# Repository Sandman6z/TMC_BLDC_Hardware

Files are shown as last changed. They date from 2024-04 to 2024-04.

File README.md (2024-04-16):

# TMC_BLDC_Hardware
TMC_BLDC 电路板部分

## TMC_BLDC
[TMC_BLDC 软件部分](https://github.com/Sandman6z/TMC_BLDC)

[TMC_BLDC HAL](https://github.com/Sandman6z/TMC_BLDC_HAL)

## BUGList:
- v1.1

| No. | BUG | Check |
| :-: | --- | :---: |
|  1  | add 12V, 5V, 3.3V test pad | √ |
|  2  | remove HALL | × |
|  3  | remove Q8 | |
|  4  | remove R65 | √ |
|  5  | Change PMOS package (Q1), Rgs (R27), Rg (R24), R14, R15 | √ |
|  6  | Crystal & capacitor package | √ |
|  7  | Inner Power layer shrinks 15mil | √ |
|  8  | LDO current change from SOT-223 to SOT-89 | √ |
|  9  | Add a current sense resistor to one phase due to DC offset | √ |
| 10  | Consider adding a power input fuse | |
| 11  | Replace reset circuit with CAT809 chip | √ |
| 12  | Add a resistor in series with an active crystal oscillator, and paralleling a large capacitor with a FB | |
| 13  | Add an LED in a specific location if have space | |
| 14  | Add Turbo Temp Port | × |
| 15  | Add TMC Debug Port | √ |

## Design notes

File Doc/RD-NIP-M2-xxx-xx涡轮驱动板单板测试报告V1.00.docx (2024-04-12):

| | | 文件级别： 机密 / Confidential | | 共 10 页

项目名称 / Project Name:

NIP

文件名称Doc. Name/编号NO:

涡轮驱动板单板测试大纲/ RD-NIP-M2-xxx-xx

相 关 文 档 / Refer Document
文件编号/Document NO | | 文件名称/Document Name | | | | 版本/Rev.
/ | | 硬件系统设计说明 | | | | 1.00
/ | | / | | | | /
/ | | / | | | | /

文 档 记 录 / Document History
版本/Rev. | 编制/日期 Author/Date | 审核/日期 Checked/Date | | 审核/日期 Checked/Date | 批准/ 日期Approved/Date
1.00

谊安公司（非公开）版权所有

本文件为谊安公司的专有资料。任何对本文件的使用、复制、或发布行为均是明确禁止的，除非本公司特殊批准，否则将被视为侵犯本公司的权利和利益。

©AEONMED CORP. (UNPUBLISHED)ALL RIGHTS RESERVED

This material is the proprietary information of Aeonmed Corp. and any use, reproduction, or distribution of the material contained herein, unless specifically authorized by Aeonmed Corp., is expressly forbidden and would violate the rights and interests of Aeonmed Corp..

版本 | 描述 | 编制/日期
1.00 | 初始版本 | 张宝宁 2024.1.25

# 目录

# 第1章 设备与环境

## 1.1 测试设备

序号 | 测试设备 | 数量
| 稳压电源 | 1台
| 数字万用表 | 1台
| 示波器 ，500M带宽，具有存储功能 | 1台
| 测温仪 | 1台
| PC机及监控软件 | 1台
| 信号发生器 | 1台
| 直流电源分析仪 | 1台
| 测试工装（NIP电源板V2.00，压力传感器160MDAA5，瑞士涡轮U65HN-024KS-6，风扇12V0.5A四线） | 1套
| 热风枪 | 1台

## 1.2 电路板硬件软件信息

序号 | 栏目 | 详细信息
| 硬件电路版本 | 45200xxxx #NIP涡轮驱动板V2.00 SN：
| 测试软件版本 | TMC_BLDC_ NIP涡轮驱动板V2.00
| 其它软件 | 无

## 1.3 测试环境

除非特别声明，一般测试环境为：

温度：20～25摄氏度

湿度：30％～85％

高度：－100～＋100m

# 第2章 测试内容

## 2.1 电压测试

测试涡轮驱动板各电源电压。

测试栏目 | 判据 | 测试数值 | 结果
VIN | 电压：24.7V±1% | 24.43V | PASS

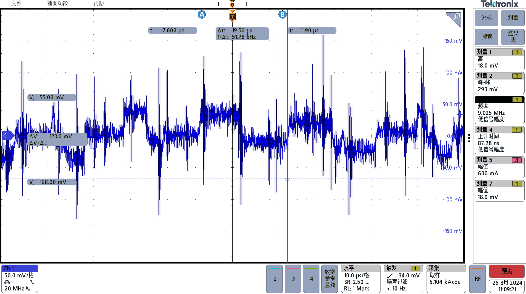
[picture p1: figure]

12V | 12±0.2V 纹波：20MHz带宽<120mV，记录数值和波形 500MHz带宽只记录数值和波形 | 12.21V | 纹波波形异常 Vp-p = 290mV

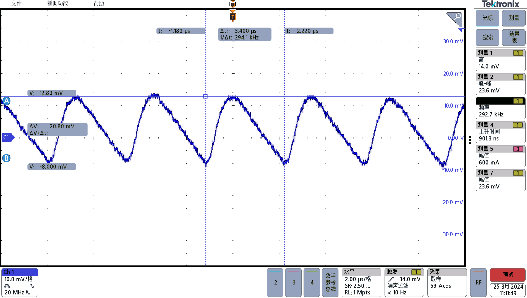
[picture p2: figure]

5V | 5±0.1V 纹波：20MHz带宽<50mV，记录数值和波形 500MHz带宽只记录数值和波形 | 5.06V | PASS Vp-p = 23.6mV

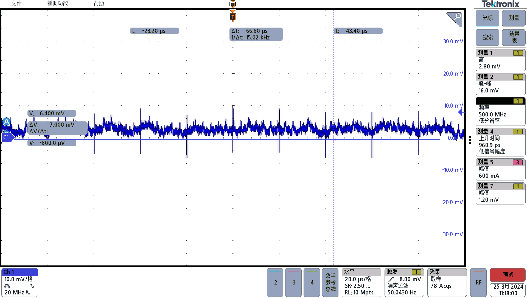
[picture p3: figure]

3.3V | 3.3±0.1V 纹波：20MHz带宽<33mV，记录数值和波形 500MHz带宽只记录数值和波形 | 3.28V | PASS Vp-p = 16mV

## 2.2 转速测试

控制输入0.5-4.5V电压，对应线性关系，6667rpm到60000rpm转速，误差±2%（对空吹时最高转速>50000rpm即合格）。

待测电压V/转速理论值rpm | 测试值对空rpm | 误差% | 测试值堵死rpm | 误差% | 结果
0.5V/6667 | 6666 | -0.015% | 6666 | -0.015%
1.0V/13333 | 13332 | -0.008% | 13332 | -0.008%
1.5V/20000 | 19998 | -0.010% | 20004 | 0.020%
2.0V/26667 | 26664 | -0.011% | 26670 | 0.011%
2.5V/33333 | 33336 | 0.009% | 33354 | 0.063%
3.0V/40000 | 39996 | -0.010% | 40002 | 0.005%
3.5V/46667 | 46656 | -0.024% | 46674 | 0.015%
4.0V/53333 | 53304 | -0.054% | 53334 | 0.002%
4.5V/60000 | 55770 | -7.050% | 57090 | -4.850%

## 2.3 电流波形测试

设定涡轮一定转速，使用示波器电流探头测试任意一个相线的电流波形，应为近似正弦波，记录三个不同转速下的波形。

转速 | 波形 | 结果

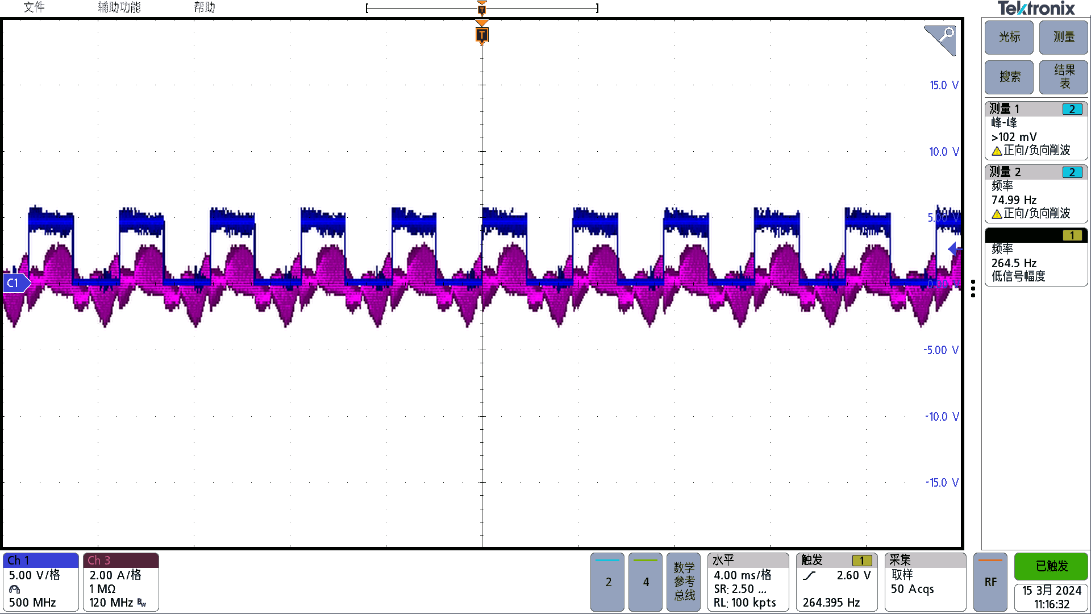
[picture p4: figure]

16000

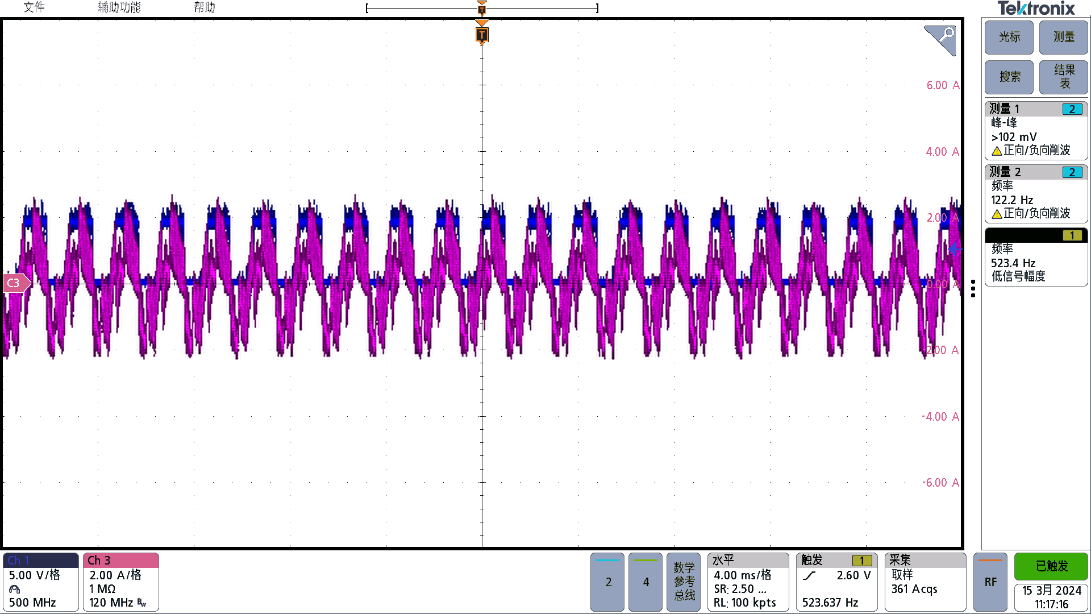
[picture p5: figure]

30000

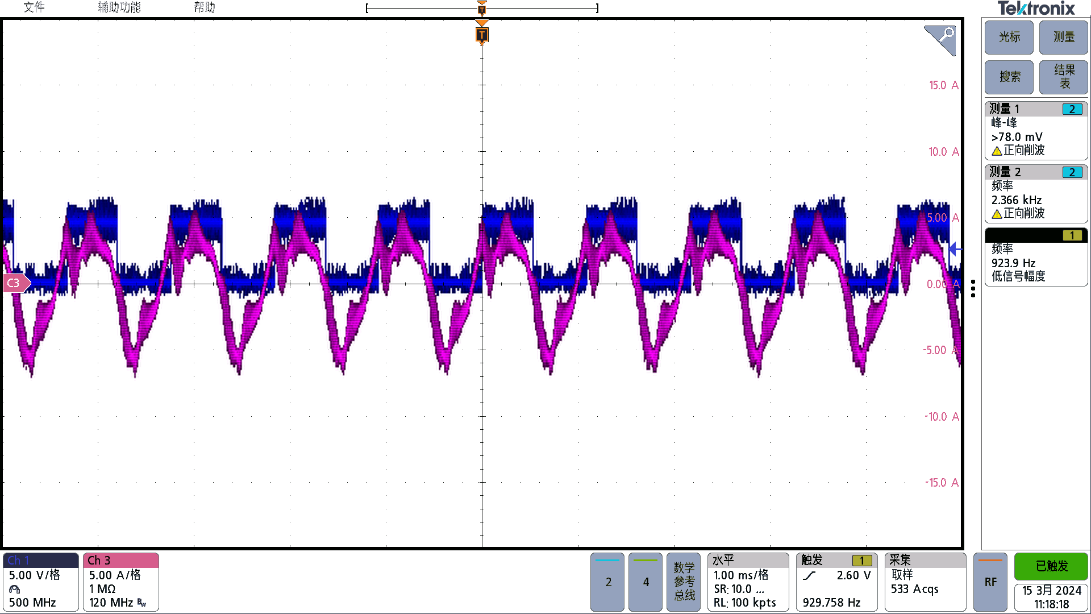
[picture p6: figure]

60000

## 2.4 加减速时间测试

将驱动器通过仿真器连接驱动测试软件，涡轮出气口接压力传感器，用示波器测量转速从0切换到60000rpm过程中传感器输出电压的波形曲线，记录电压上升时间，小于300ms合格。

转速 | 波形 | 结果

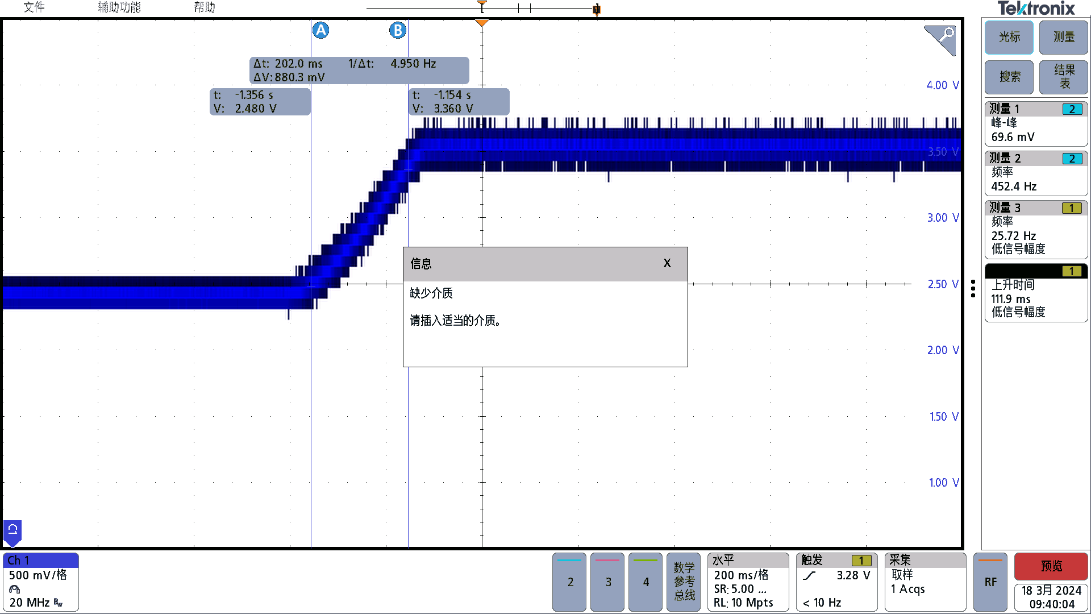
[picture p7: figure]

0-60000 | | 202ms 通过

## 2.5 电源电压冲击测试

设定涡轮进行速度切换（6000（2S）-60000（2S）-6000（2S）-60000（2S）），测试切换过程中VIN以及VM的波动。（使用NIP系统电源板供电进行测试）

测试值 | 状态及判据 | 波形 | 结果
VIN | 加速过程 合格判据ΔV<1V | 万用表测0.2V | PASS

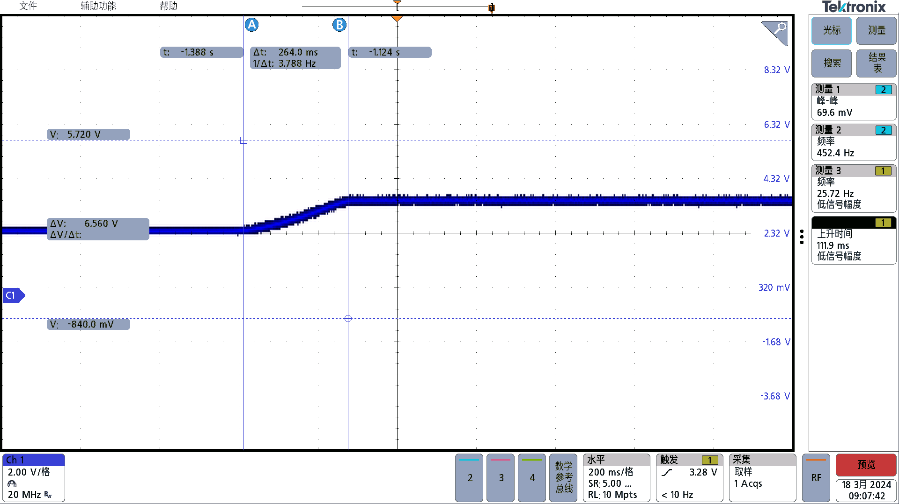
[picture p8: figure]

| 刹车过程 合格判据ΔV<2V | | PASS

## 2.6 温升测试

涡轮对空吹，持续进行转速（6000（2S）-60000（2S）-6000（2S）-60000（2S））的切换过程，持续24h或至热平衡，用红外成像仪观察，读取发热器件温升，附红外热像仪图。

环境温度：

时间(h) | 刹车MOS管 温升<70℃ | 驱动MOS管 温升<70℃ | 刹车电阻 温升<70℃ | 驱动电感 温升<70℃ | 涡轮 温升<20℃ | 结果
0 | | | | | | PASS
25.2 | | | | | | PASS

涡轮对空吹，进行30min最高转速持续温升测试，用红外成像仪观察，读取发热器件温升，附红外热像仪图。

环境温度：

时间 | MOS管温度 温升<70℃ | 驱动电感 温升<70℃ | 涡轮 温升<20℃ | 结果

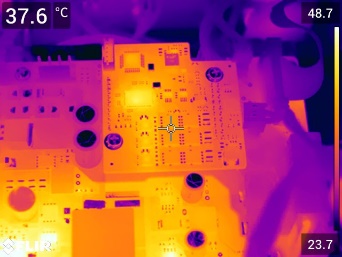
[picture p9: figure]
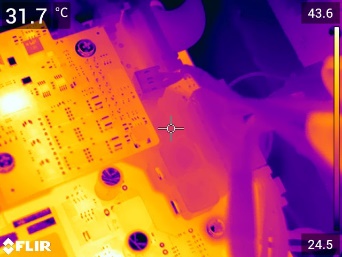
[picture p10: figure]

0 | 37.6 | 31.7 | 27 | PASS

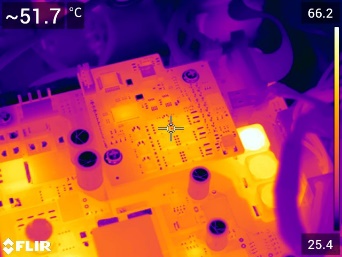
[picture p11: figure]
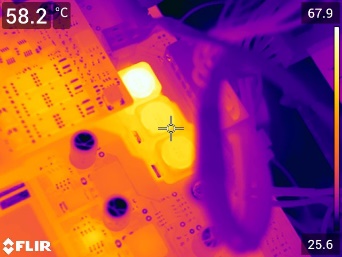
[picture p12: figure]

5 | 51.7 | 67.9/58.2 | 29.7 | PASS

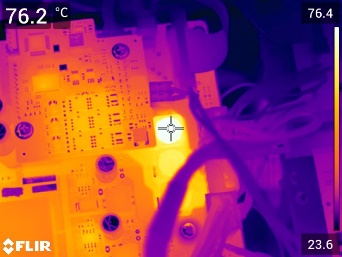
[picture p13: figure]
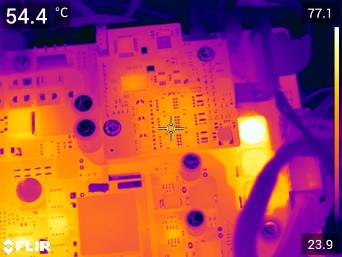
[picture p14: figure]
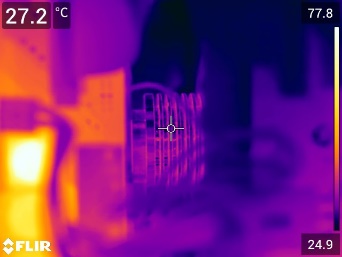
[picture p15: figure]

10 | 54.4 | 76.2/66.9 | 27.2 | PASS

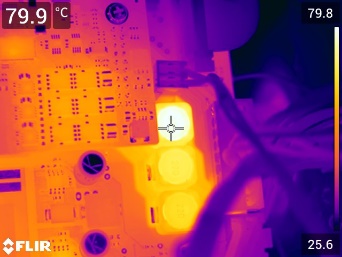
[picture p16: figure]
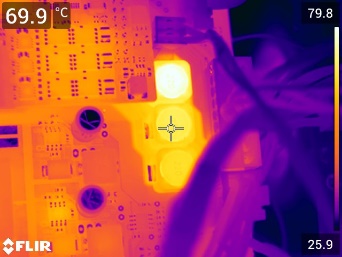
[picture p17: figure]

15 | 55.1 | 80.2/70 | 34.1 | PASS

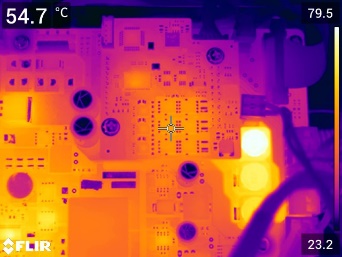
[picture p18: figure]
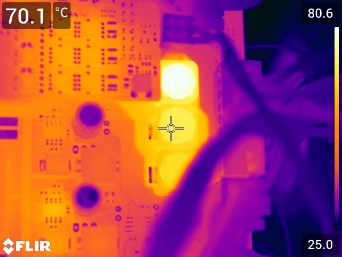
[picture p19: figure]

20 | 54.7 | 80.3/71.5 | 30.3 | PASS

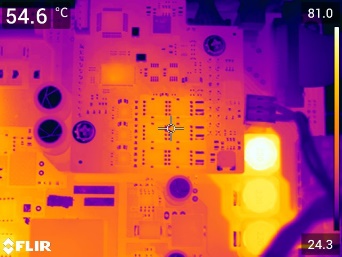
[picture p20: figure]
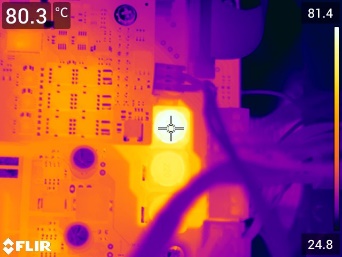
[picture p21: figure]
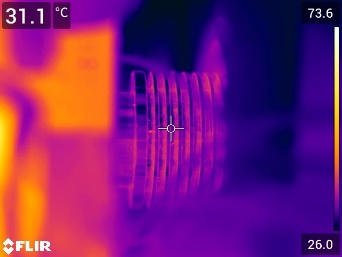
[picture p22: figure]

25 | 55.7 | 80.4/71.8 | 29 | PASS

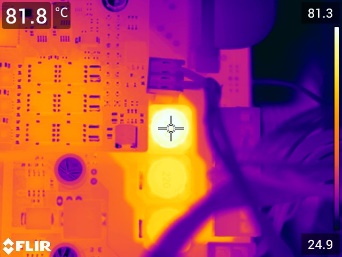
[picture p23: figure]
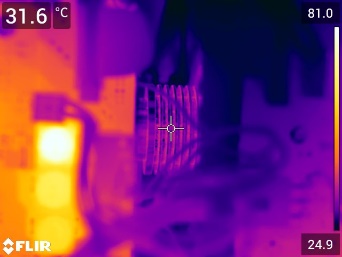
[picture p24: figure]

30 | 55.4 | 81.8/70.7 | 32.8 | PASS

## 2.7 状态以及故障测试

状态 | 状态信号 | 状态标识位 | 结果
欠压 | POWER | 0故障1正常 | PASS
过压 | POWER | 0故障1正常 | PASS
涡轮超温 | TEMSTATUS | 0故障1正常 | N/A
涡轮转速 | TURSPEED | 能监测，误差±5% | PASS
涡轮温度 | TEM | 能监测，误差±5% | N/A
输入电压 | PWBUS | 能监测，误差±5% | PASS
电机电压 | VM | 能监测，误差±5% | PASS

## 2.8 电源保护测试

测试电路的各种保护功能

电源状态 | 测试方法 | 通过标准 | 结果
反接 | 将涡轮驱动器电源反向接入，通电，观察涡轮驱动板，将涡轮驱动器电源正向接入，通电，观察涡轮驱动板 | 反向接入：涡轮驱动板无烧毁，冒烟等不正常现象 正常接入：涡轮驱动板运行上电，可以驱动涡轮转动 | N/A
过流 | 将涡轮驱动板连接涡轮线圈的接口短路，通电，输入转速信号，观察涡轮驱动器 | 短路：保险管断开，无冒烟的现象 正常接入：修复保险丝后，涡轮驱动板运行上电，可以驱动涡轮转动 | N/A
过压 | 使涡轮转动，缓慢升高输入电压，观察当涡轮停转时，输入电压值 | 停转电压：34-36V | PASS
欠压 | 使涡轮转动，缓慢减低输入电压，观察当涡轮停转时，输入电压值 | 停转电压：17-19V | PASS
超温 | 使涡轮转动，拔掉测温电阻或制造高温 | 超温时涡轮停转，恢复后涡轮正常转动 | N/A

## 2.9 噪声测试

将驱动器和荷兰涡轮放置于静音室，音频探头放置于进气口1M的距离，设置转速，测量噪音。

环境噪声：41.8 dB(A)

测试条件 | 转速rpm | 通过标准 | 结果
对空吹 | 60000 | <80dB(A)
堵死 | 60000 | <80dB(A)

见下表：

转速（rpm） | 对空dB(A) | 堵死dB(A)
15770 | 45.9 | 42.6
31300 | 60.7 | 52.8
46770 | 70.3 | 58.8
60000 | 74.2 | 61.6

# 第3章 报告分析

## 3.1 针对12V测试纹波异常问题，考虑到已暂无货源问题，改用TI电源芯片，性能更稳定，下版本修改方案后进行再次测试；

## 3.2 最高转速达不到接近60000rpm，由于调试机可能存在漏气的问题，非驱动板问题，但未影响BDU调试，等下版重新装机，配合新涡轮驱动板再测试；

## 3.3 针对温升测试PD板某一路电感温度过高问题，怀疑是该路没有分压，导致有直流分量，作用发热导致，下版修改；

## 3.4 涡轮噪声进行分体测试，标准中为整机噪声结果，需下版装好整机并核查气路气密性后进行测试；

3.5 存在一些检查项该版本未设计，下版增加功能。

机密文件，知识产权属谊安公司所有 第 2 页 共 10 页

涡轮驱动板单板测试大纲/ RD-NIP-M2-xxx-xx（1.00）

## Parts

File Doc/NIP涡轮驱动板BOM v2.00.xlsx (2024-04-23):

Line # | Name | Description | Designator | Quantity | Manufacturer 1 | Manufacturer Part Number 1 | Manufacturer Lifecycle 1 | Supplier 1 | Supplier Part Number 1 | Supplier Unit Price 1 | Supplier Subtotal 1
 | 10nF ±10% 50V X7R | CL05B103KB5NNNC | C1, C43 | 2
 | 100nF ±10% 50V X7R | CL05B104KB54PNC | C2, C6, C7, C8, C9, C10, C11, C12, C13, C14, C15, C16, C17, C18, C19, C20, C21, C32, C33, C34, C39, C40, C41, C44, C46, C47, C51, C53, C54, C57, C61, C62 | 32
 | 470nF ±10% 10V X7R | CL05B474KP5NNNC | C3 | 1
 | 4.7uF ±10% 10V X5R | CL05A475KP5NRNC | C4, C5 | 2
 | 1uF ±10% 6.3V X7R | CL05B105KQ5NQNC | C22 | 1
 | 4.7uF ±10% 50V X7R | CL32B475KBUYNNE | C23, C28, C30 | 3
 | 1uF ±10% 25V X7R | CL10B105KA8NNNC | C24, C25, C26 | 3
 | 100nF ±10% 50V X7R | CL10B104KB8NNNC | C27, C29, C31 | 3
 | 2.2nF ±5% 50V X7R | CL05B222JB5NNNC | C35, C42 | 2
 | 100pF ±5% 50V C0G | CL05C101JB5NNNC | C36, C37, C38 | 3
 | 2.2uF ±10% 50V X5R | CL10A225KB8NNNC | C45, C52 | 2
 | 10uF ±20% 25V X5R | CL10A106MA8NRNC | C48, C49, C55, C56 | 4
 | 1nF ±10% 50V X7R | CL05B102KB5NNNC | C58, C59 | 2
 | 10uF ±20% 10V X5R | CL05A106MP5NUNC | C60, C63 | 2
 | BAT54S | 品牌：NXP，型号：BAT54S，0.11A,30V，ROHS | D1, D9 | 2
 | SKL110 | 品牌：DIOTEC，型号：SKL110，1A，100V，ROHS | D2, D4, D6 | 3
 | BZX384-B13 | 品牌：NXP，型号：BZX384-B13，13V，SOD-323，ROHS | D3, D5, D8 | 3
 | SS14 | 直流反向耐压(Vr):40V;平均整流电流(Io):3A;正向压降(Vf):500mV@3A; | D7 | 1
 | 30R@100MHz 3A | 品牌：TDK，型号：MPZ1608S601A , 600 ohm@100MHz ，1 A，25%，ROHS | FB1 | 1
 | SN74LVC3G17DCUR | 品牌：TI，型号： 74LVC3G17, 1.65 V to 5.5 V, VSSOP-8，，ROH | IC1 | 1
 | TMC4671 | 品牌：TRINAMIC，型号：TMC4671，ROHS | IC200 | 1
 | JST_PH 2.00-5 | 品牌：JST 型号：B5B-PH-K-S，直插，间距2.00，5pin | J1 | 1
 | 62000821121 | WR-PHD Pin Header, THT, Vertical, pitch 2mm, 2 Row, 8P | J2 | 1
 | 10uH, 3.3A | 74438367100 WE-MAPI, size 5030, 10uH, 3.3A, 70.2mOhm | L1 | 1
 | 15uH, 1.9A | 74438356150 WE-MAPI, size 4020, 15uH, 1.9A, 230mOhm | L2 | 1
 | BSC027N04LSG | 品牌：INFINEON，型号： BSC027N04LSG，40V，100A，ROHS | Q1, Q2, Q3, Q4, Q5, Q6 | 6
 | AO3410 | AO3410 | Q7, Q9 | 2
 | SI7463ADP-T1-GE3 | 类型 P沟道 漏源电压(Vdss) 40V 连续漏极电流(Id) 46A 功率(Pd) 5W；39W 导通电阻(RDS(on)@Vgs,Id) 10mΩ@15A,10V 阈值电压(Vgs(th)@Id) 2.3V@250uA | Q8 | 1
 | 100KΩ ±1% 62.5mW | RC0402FR-07100KL | R1, R36 | 2
 | 1.5KΩ ±1% 62.5mW |  | R2, R16 | 2
 | N/C |  | R3 | 1
 | 51Ω ±1% 62.5mW |  | R4 | 1
 | 10KΩ ±1% 62.5mW |  | R5, R6, R7, R8, R9, R29, R30, R33, R58 | 9
 | 5.1KΩ ±1% 62.5mW |  | R10 | 1
 | 2.2Ω ±1% 62.5mW | Resistor | R11, R20, R31 | 3
 | 2.2Ω ±1% 67.5mW | Resistor | R12, R15, R23, R26, R35, R39 | 6
 | 10KΩ ±1% 62.5mW | Resistor | R13, R14, R24, R25, R37, R38 | 6
 | 10kΩ ±1% 62.5mW | Resistor | R17, R18, R19, R21, R62, R64, R66 | 7
 | 3.3KΩ ±1% 62.5mW |  | R27 | 1
 | NTCS0603E3103FHT | 品牌：VISHAY，型号：NTCS0603E3103FHT，10K@25℃, 1%，B=3960,ROHS | R28 | 1
 | 100Ω ±1% 62.5mW |  | R32, R34, R63, R71 | 4
 | 4mΩ ±1% 3W | PA2512FKF7T0R004E | R40, R41 | 2
 | 1KΩ ±1% 62.5mW |  | R42, R46, R47, R48 | 4
 | 62KΩ ±1% 62.5mW |  | R43 | 1
 | 20KΩ ±1% 62.5mW |  | R44 | 1
 | 30KΩ ±1% 62.5mW |  | R45 | 1
 | 1kΩ ±1% 62.5mW | Resistor | R49, R54 | 2
 | 7.5mΩ ±1% 2W | PA2512FKF7W7U5E 7.5mOhms 2W 100PPM/C 1 % 2512 | R51, R55, R56 | 3
 | 1kΩ ±1% 62.5mW |  | R57 | 1
 | 1KΩ ±1% 62.5mW | Resistor | R65 | 1
 | 100kΩ ±1% 62.5mW | RC0402FR-07100KL | R67, R69 | 2
 | 5.23kΩ ±1% 62.5mW | RC0402FR-075K23L | R68 | 1
 | 13.7kΩ ±1% 62.5mW | RC0402FR-0713K7L | R70 | 1
 | 3.3kΩ ±1% 62.5mW |  | R72 | 1
 | 1MΩ ±1% 62.5mW |  | R73 | 1
 | 10KΩ ±1% 62.5mW |  | RP2, RP3 | 2
 | 330Ω ±1% 62.5mW |  | RP4, RP5, RP6 | 3
 | 100Ω ±1% 62.5mW |  | RP7, RP8 | 2
 | 22Ω ±1% 62.5mW |  | RP9 | 1
 | SRV05-4.TCT | 品牌：SEMTECH ，型号：SRV05-4.TCT，ROHS | TVS1 | 1
 | STM32F103CBU6 | STM32F103CBU6 | U1 | 1
 | CAT803STBI−GT3 |  | U2 | 1
 | LM5109BSD/NOPB | 品牌：TI，型号：LM5109BSD/NOPB，ROHS | U3, U4, U5 | 3
 | INA381A3IDGSR | 品牌：TI，型号：INA381A1IDGSR，ROHS | U6 | 1
 | AD8418ABRMZ | 品牌：ADI，型号：AD8418ABRMZ，ROHS | U7, U8 | 2
 | mus50/5/4q | 品牌：长江（CJT） A: A2005WVA-12P B: A2541WV-2x10P | U9 | 1
 | LMR51430YFDDCR | 输入电压 4.5V~36V 输出电压 600mV~34.2V 输出电流(最大值) 3A 开关频率 1.1MHz 工作温度 -40℃~+150℃ 静态电流(Iq) 40uA | U10, U11 | 2
 | TLV333IDBVR | 品牌：TI，型号：TLV333IDBVR,SOIC-8,–25°~+85°C,单运放，ROHS | U12 | 1
 | 1117-3.3 | SOT-89-3 | U13 | 1
 | 8MHz ±10ppm_10pF | 品牌：TAITIEN,型号：（OX系列）OXETELJANF-8.000000，尺寸：3.2 x 2.5mm | X1 | 1 | Abracon | ABM3B-8.000MHZ-10-1-U-T | Volume Production | Digikey | 535-9721-2-ND | 0.45447 | 454.47
 | 25.000MHz ±10ppm_10pF | YSO110TR 25MHZ 1.8V-3.3V ±10PPM -40~85℃（±20PPM) CMOS 型号：OT3JI-111-25M | Y1 | 1

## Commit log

2023-11-27 update to github
    [#NIP涡轮驱动板-1.SchDoc, #NIP涡轮驱动板-2.SchDoc, #NIP涡轮驱动板-3.SchDoc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]
2023-12-28 find some bugs, wrote by the question part.
    [#NIP涡轮驱动板-4.SchDoc, #NIP涡轮驱动板-Power.SchDoc]
2024-04-09 1. change LDO 2. add calculate current sideby DCDC
    [#NIP涡轮驱动板-1.SchDoc, #NIP涡轮驱动板-2.SchDoc, #NIP涡轮驱动板-3.SchDoc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]
2024-04-10 1. add current resistor; 2. adjust DCDC chip; 3. add LDO SOT89
    [#NIP涡轮驱动板-DRIVE.SchDoc, #NIP涡轮驱动板-Power.SchDoc, #NIP涡轮驱动板-Sense.SchDoc]
2024-04-11 Resurrect the TMC debug port
    [#NIP涡轮驱动板-Power.SchDoc, #NIP涡轮驱动板-TMC.SchDoc, NIP涡轮驱动板BOM.xlsx]
2024-04-11 add DC-DC part
    [#NIP涡轮驱动板-Power.SchDoc]
2024-04-12 change preDriver MOS Gate RES
    [#NIP涡轮驱动板-DRIVE.SchDoc, #NIP涡轮驱动板-MCU.SchDoc, #NIP涡轮驱动板-Power.SchDoc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]
2024-04-15 adjust DC-DC layout
    [#NIP涡轮驱动板-DRIVE.SchDoc, #NIP涡轮驱动板-Power.SchDoc]
2024-04-15 adjust component to 0402
    [#NIP涡轮驱动板-DRIVE.SchDoc, #NIP涡轮驱动板-Sense.SchDoc]
2024-04-16 move all part, what a messsss........
    [#NIP涡轮驱动板-DRIVE.SchDoc, #NIP涡轮驱动板-MCU.SchDoc, #NIP涡轮驱动板-Power.SchDoc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]
2024-04-16 change stm32f103cbu6
    [#NIP涡轮驱动板-DRIVE.SchDoc, #NIP涡轮驱动板-MCU.SchDoc, #NIP涡轮驱动板-MCUnew.SchDoc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]
2024-04-17 这个版本是layout中的，但是电流采样和霍尔信号处理的两部分layout还没有混到一起，如有需要，可以回退到此版本进行参考
    [#NIP涡轮驱动板-Power.SchDoc, #NIP涡轮驱动板-Sense.SchDoc]
2024-04-17 all part inside the board, ready change layer to 6git add .!
    [#NIP涡轮驱动板-MCUnew.SchDoc, #NIP涡轮驱动板-TMC.SchDoc]
2024-04-17 already change layer to 6
    [#NIP涡轮驱动板-DRIVE.SchDoc]
2024-04-18 almost finish layout, let Cai check.
    [#NIP涡轮驱动板-MCUnew.SchDoc, #NIP涡轮驱动板-Power.SchDoc]
2024-04-19 let Sunke check.
    [#NIP涡轮驱动板-Power.SchDoc, #NIP涡轮驱动板-TMC.SchDoc]
2024-04-22 FINISH this version layout
    [#NIP涡轮驱动板-Power.SchDoc, #NIP涡轮驱动板-TMC.SchDoc]
2024-04-23 finish layout adjust. Ready to adjust silk.
    [#NIP涡轮驱动板-Power.SchDoc]
2024-04-23 FINISH design & BOM
    [#NIP涡轮驱动板-DRIVE.SchDoc, #NIP涡轮驱动板-MCUnew.SchDoc, #NIP涡轮驱动板-Power.SchDoc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]
2024-05-06 change wrong 2.2Ω ±1% 67.5mW to 62.5mW
    [#NIP涡轮驱动板-1.SchDoc, #NIP涡轮驱动板-2.SchDoc, #NIP涡轮驱动板-3.SchDoc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]
2024-06-14 change wrong MCU crystal capacitor from 100nF -> 10pF
    [#NIP涡轮驱动板-MCUnew.SchDoc, #NIP涡轮驱动板BOM v2.00.xlsx, NIP涡轮驱动板BOM v1.0.xlsx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]
2024-06-14 remove no useful pcblib
    [130020900#NIP_PD_电路板印制板.PcbLib, 452005691#NIBP涡轮驱动板V2.00.PcbLib, 452006250-3#NIBP涡轮驱动板V2.001.PcbLib]
